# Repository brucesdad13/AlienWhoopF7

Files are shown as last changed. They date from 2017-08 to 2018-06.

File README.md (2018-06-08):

IMAGE AlienWhoop F7 Flight Controller Welcome

# AlienWhoopF7 Features :alien:
AlienWhoop flight controller for Tiny Whoop, Blade Inductrix, Eachine, BetaFPV, and other micro brushed quadcopter frames. Best in class flight controller running BetaFlight or Butterflight--surface mount soldering required.

* Choice of the top performing ARM processors: 
  * High-performance ST Microelectronics ARM Cortex-M4 core F4 168 MHz CPU
  * High-performance ST Microelectronics ARM Cortex-M7 core F7 216 MHz CPU
* Choice of top performing motion processors: 
  * Invensense MPU-6500 Six-Axis (Gyro + Accelerometer) low power consumption MEMS MotionTracking™ Device
  * Invensense MPU-9250 Nine-Axis (Gyro + Accelerometer + Compass) low power consumption MEMS MotionTracking™ Device
* Latest BetaFlight firmware running the ALIENWHOOPF4 target
* Butterflight firmware supported (iNav under final testing)
* Overkill power MOSFETs capable of extreme brushed motor insanity (6mm, 7mm, 8mm, 8.5mm, and 10mm coreless scream)
* Multiple UARTs for receivers and other devices (e.g. LED strip, beeper)
* Dedicated UART with inverter for FrSky and Futaba SBUS
* UART pads on top conveniently located for SmartAudio VTX control
* Blackbox logging via onboard dataflash chip
* Note: pilots must supply external receiver. Officially supporting FrSky XM, XM+, R-XSR (SBUS,F.PORT), LemonRX DSM2 and DSMX (SBUS), and FlySky FS-A8S (iBUS) satellites.
* 0.8mm 2oz Copper ENIG (gold) finish purple PCBs from OSH Park recommended

## DIY Flight Controller :alien:
If you fancy doing it yourself (DIY), and have the right equipment and patience, building an AlienWhoop from scratch can be tremendously satisfying--though not for the faint of heart. After doing your homework the first step is to place an order for blank PCBs from [OSH Park](https://oshpark.com/shared_projects/p4hs6DbI):
* We recommend ordering the 2oz copper 0.8mm thickness PCB
  * *It takes about three weeks to make the thin boards which allows plenty of time to order components from the bill of materials in the resources folder.*
  * **Please note there are slight changes to the bill of materials (BOM) depending which MCU you choose (F4 vs F7). These MCUs are not 100% pin compatible.**
   * F4: components C7 and C10 place 4.7uF ceramic capacitors and C15 substitute 0 ohm resistor (0R).
   * F7: components C7, C10, and C15 place 4.7uF ceramic capacitor.

## Official AlienWhoop pages :alien:
AlienWhoop has many ways for you to stay engaged. Please Like and/or Follow Us for regular updates in your status feed related to AlienWhoop, DIY electronics, and micro brushed quadcopter related posts.
* http://fb.me/alienwhoop/ Facebook
* http://alienwhoop.us/ News and products
* http://alienwhoop.us/git-config CLI diff files for Betaflight and Butterflight
* http://alienwhoop.us/discord Join our Discord chat and hang out with the community or ask questions

## See the AlienWhoop in action on YouTube :alien:

IMAGE VelcroFPV Tinywhoop Invitational 2018 Best Run (https://www.youtube.com/watch?v=_v07IYvKqXY)

IMAGE VelcroFPV AlienWhoop Build (https://www.youtube.com/watch?v=SfvL05S8X-s&t=30s)

May this work be of benefit and bring much joy and happiness!

## Acknowledgements :alien:

AlienWhoop V2.1 Dev Team:
* Charles Stevenson (brucesdad13)
* Travis Schrock (NotFastEnuf)
* Brian Pichardo (VelcroFPV)
* Michael Montiverdi (MontiFPV)

Deep bows of appreciation and thanks to Lance for his original work and tremendous
generosity in releasing his labor of love for the benefit of all flight controller
enthusiasts. Check out AlienWhoop's ancestry in our preserved copy of Lance's original AlienFlight
github repository of open source hardware flight controllers: the [Classic FC aka Classic Narrow](https://github.com/brucesdad13/AlienFlightArchive/blob/master/Flight-Controllers/Classic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), [F3 Quad FC](https://github.com/brucesdad13/AlienFlightArchive/blob/master/Flight-Controllers/F3-V1/F3-Quad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), [F3 Hexa FC](https://github.com/brucesdad13/AlienFlightArchive/blob/master/Flight-Controllers/F3-V1/F3-Hexa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), and [F3 Octo FC](https://github.com/brucesdad13/AlienFlightArchive/blob/master/Flight-Controllers/F3-V1/F3-Octo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).
*As of late July 2017, the original www.alienflight.com site is no longer in operation.

Equally deep bows to Jesse Perkins, creator of Tiny Whoop, and the source of inspiration and love for tiny brushed quads.
* http://www.tinywhoop.com/ ~
* https://www.facebook.com/groups/tinywhoop/ ~

~ Please note: **AlienWhoop** is not affiliated with nor endorsed by AlienFlight or forks of Lance's work such as AlienFlight NG. The use of Alien in the name and the alien head vector graphic used on the board silkscreen are nods to the lineage of this remix and to the work of Lance and others who created the conditions for this project to arise. Likewise, AlienWhoop is not affiliated with nor endorsed by Tiny Whoop. The Whoop in the name comes from Jesse Perkin's fantastic Tiny Whoop ("a small first-person-view aircraft that truly allows you to feel the gift of flight and the feeling of being tiny" [tinywhoop.com]) and is simply a nod to his efforts and the TW community worldwide.

## If you like this project and want to support further development
* https://paypal.me/AlienWhoop/ <a href="https://paypal.me/AlienWhoop/">Donate PayPal - The safer, easier way to pay online!</a>
* http://shop.alienwhoop.us/ for t-shirts and gear

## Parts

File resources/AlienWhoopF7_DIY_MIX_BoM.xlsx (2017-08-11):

Value | Device | Package | Parts/Silkscreen Label | Description | MF | MPN
.01uF | Capacitor 0.01 uF | 0603 | C3 | CAPACITOR | Murata | GRM188R71C103KA01D
.1uF | Capacitor 0.10 uF | 0603 | C2, C5, C6, C8, C9, C11, C12, C14 | CAPACITOR | Murata | GRM188R71C104KA01D
10uF | Capacitor 10.0 uF | 0805 | C1, C4 | CAPACITOR | Taiyo Yuden | JMK212AB7106KG-T
1uF | Capacitor 1.00 uF | 0603 | C13 | CAPACITOR | Murata | GRM188R71C105KA12D
4.7uF | Capacitor 4.70 uF | 0603 | C7, C10 | CAPACITOR | Murata | GRJ188C70J475KE11D
4.7uF | Capacitor 4.70 uF | 0603 | C15 | CAPACITOR | Murata | GRJ188C70J475KE11D
FDMA410NZ | MOSFET | UMLP-6 | Q2, Q3, Q4, Q5 | MOSFET 20V Single N-Ch 1.5V (9.5 amp continuous, 23 amp pulsed) | Fairchild | FDMA410NZ
1S (3.8V) | Connector JST PH 2.0 | S2B-PH-K-S | BAT | 1S LIPO connector to make PowerWhoop 2.0 pigtail w/24AWG wire and heatshrink | JST | S2B-PH-K-S
SBUS | Connector 3-pin Receiver | S3B-ZR | RX | 3 Pin Receiver (optional.. Used if not directly soldering satellite rx to through holes) | JST | S3B-ZR
105133-0011 | Vertical USB Port | 1051330011-SD | USB | Molex USB Connectors uUSB B Rec Vertical TH 2.30 | MOLEX | 105133-0011
IRLML6402 | MOSFET-P | SOT-23 | Q1 | P-Channel MOSFET | IR | IRLML6402
MPU-6500 | MPU-6500 Gyro/Acc | QFN24_PAD | U2 | Invensense MPU-6500 6-axis motion processor gyro accelerometer NO COMPASS | INVENSENSE | MPU-6500
MPU-9250 | MPU-9250 Gyro/Acc/Mag | QFN24_PAD | U2 | Invensense MPU-9250 9-axis motion processor gyro accelerometer compass | INVENSENSE | MPU-9250
2.2uH | Inductor 2.2 uH | TFM201610ALMA | L1 | Thin Film Metal Inductor substituted for Taiyo Yuden | Taiyo Yuden | TFM201610ALMA2R2MTAA
53047-0210 | Connector Brushed Motor | PICO-53047-02 | M1, M2, M3, M4 | Motor Connector | MOLEX | 53047-0210
0R | Resistor 0.00 Ohms | 0603 | C15 | RESISTOR used as Jumper | Yageo | RC0603FR-070RL
0R | Resistor 0.00 Ohms | 0603 | C7, C10 | RESISTOR used as Jumper | Yageo | RC0603FR-070RL
10K | Resistor 10K Ohms | 0603 | R1, R2, R3, R4, R5 | RESISTOR | Vishay | CRCW060310K0FKEAHP
8mhz | Resonator 8 MHz | RESONATOR_8 | Y1 | SMD Ceramic Resonators | Murata | CSTCE8M00G55-R0
BLUE | LED (blue as spec'd only!) | 0805 | LED0, LED1, PWR | SMD CHIP LED | Kingbright | APHCM2012QBC/D-F01
STM32F4/F7 | STM32F405RGT | LQFP64 | IC1 | ARM 32-bit Cortex™-M3 168 MHz CPU |  | STM32F405RGT6
STM32F4/F7 | STM32F722RET | LQFP64 | IC1 | ARM 32-bit Cortex™-M4 216 MHz CPU |  | STM32F722RET6
TPS63001 | TPS630XX-TPS63001 | VSON-N10 | U1 | Buck/Boost Converter | TI | TPS63001DRCR
AW-F4-BR-V2-PCB | AW-F4-BR-V2-PCB | PCB | PCB | PCB 0.8mm thick 2oz copper | OSH Park | AlienWhoop F7 DIY MIX
* Yellow highlighted rows are for F4 builds or in case of MPU-9250 optional upgrade for compass/mag
** LED circuits lack current limiting resistor so only specified blue LED can be used for LED0 and LED1

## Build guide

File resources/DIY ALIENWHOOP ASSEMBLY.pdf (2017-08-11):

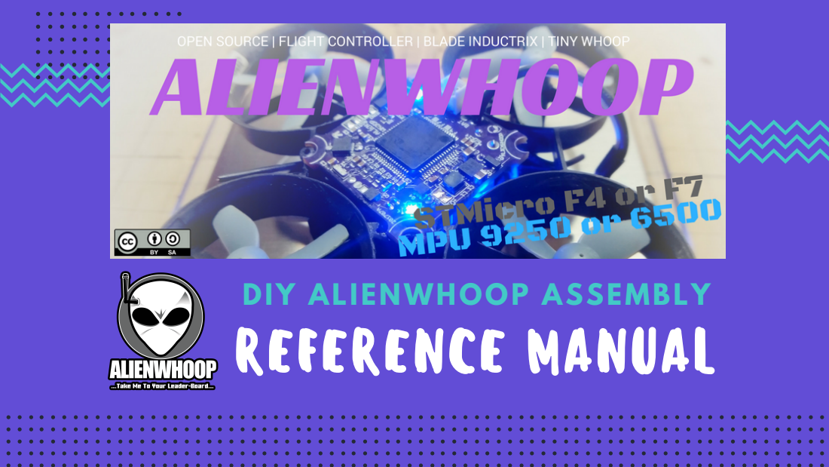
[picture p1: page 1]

DIY ALIENWHOOP ASSEMBLY
REFERENCE MANUAL

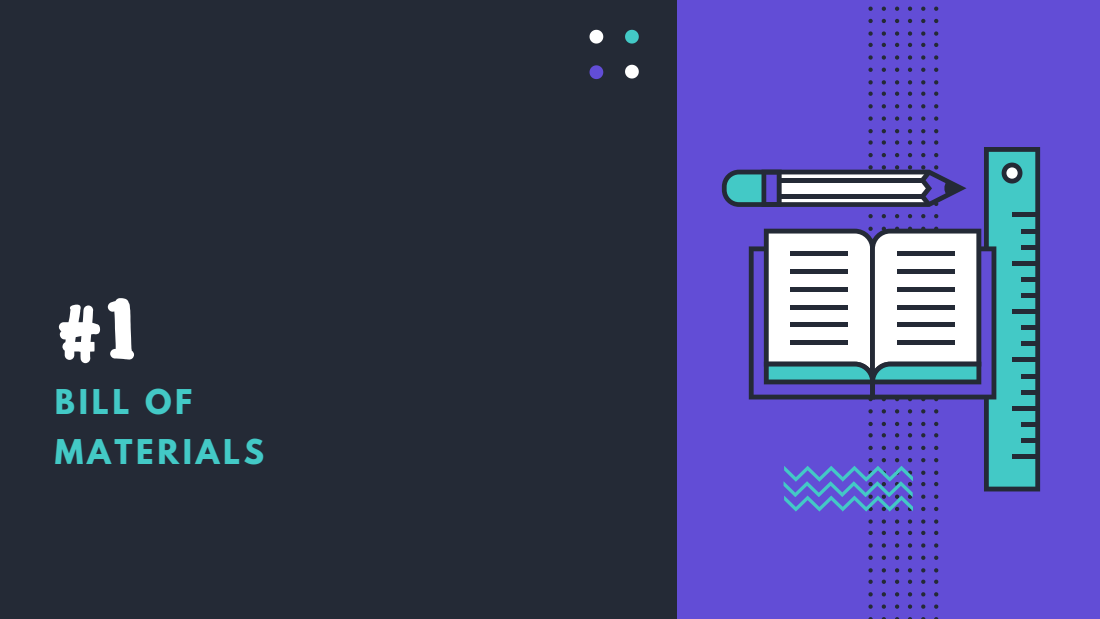
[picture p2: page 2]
BILL OF MATERIALS

# CHECK YOUR CART

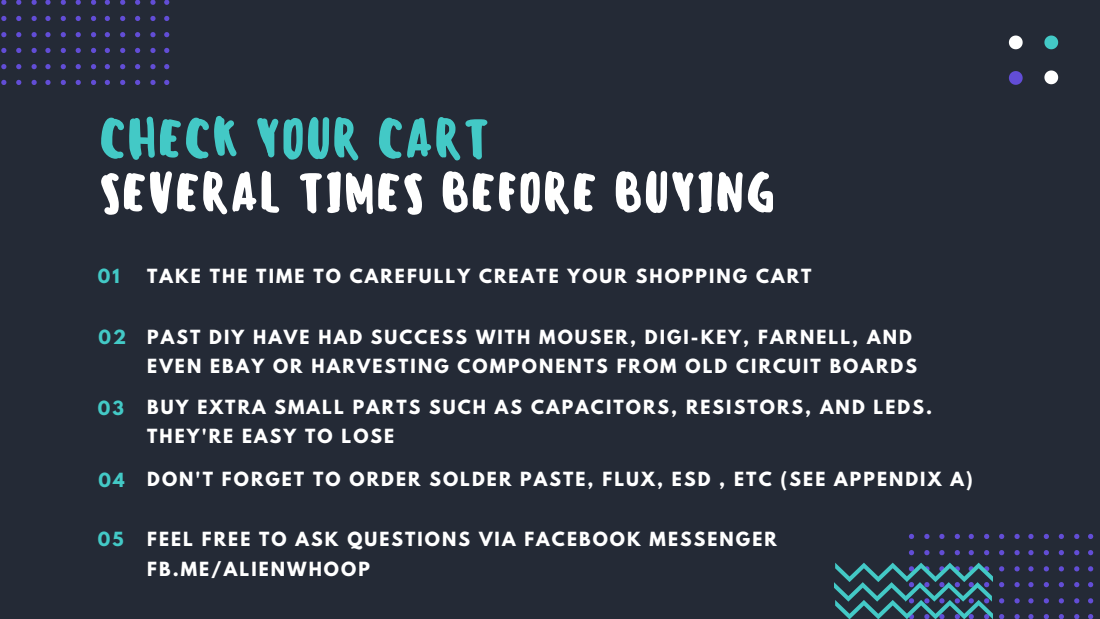
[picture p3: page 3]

SEVERAL TIMES BEFORE BUYING

01 TAKE THE TIME TO CAREFULLY CREATE YOUR SHOPPING CART

PAST DIY HAVE HAD SUCCESS WITH MOUSER, DIGI -KEY, FARNELL, AND
EVEN EBAY OR HARVESTING COMPONENTS FROM OLD CIRCUIT BOARDS
BUY EXTRA SMALL PARTS SUCH AS CAPACITORS, RESISTORS, AND LEDS.
THEY'RE EASY TO LOSE

04 DON'T FORGET TO ORDER SOLDER PASTE, FLUX, ESD , ETC (SEE APPENDIX A)

FEEL FREE TO ASK QUESTIONS VIA FACEBOOK MESSENGER
FB.ME/ALIENWHOOP

# Bill of Materials

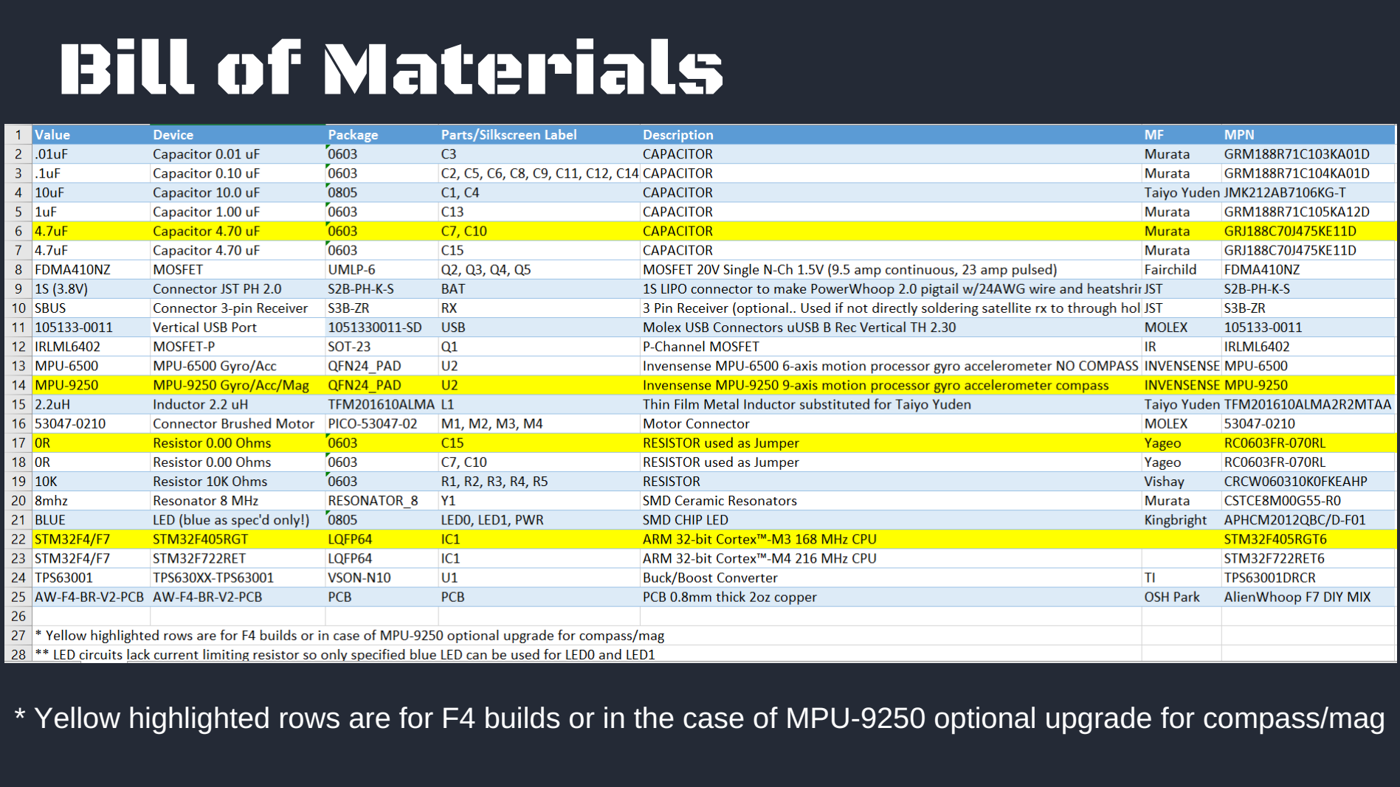
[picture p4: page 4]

* Yellow highlighted rows are for F4 builds or in the case of MPU-9250 optional upgrade for compass/mag

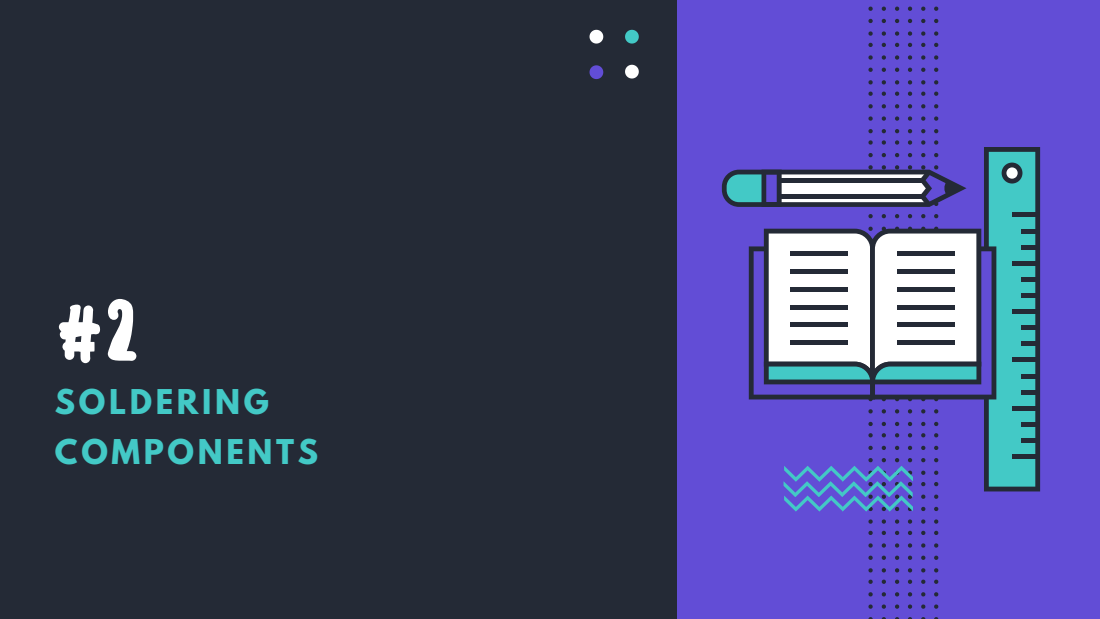
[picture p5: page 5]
SOLDERING COMPONENTS

T

O

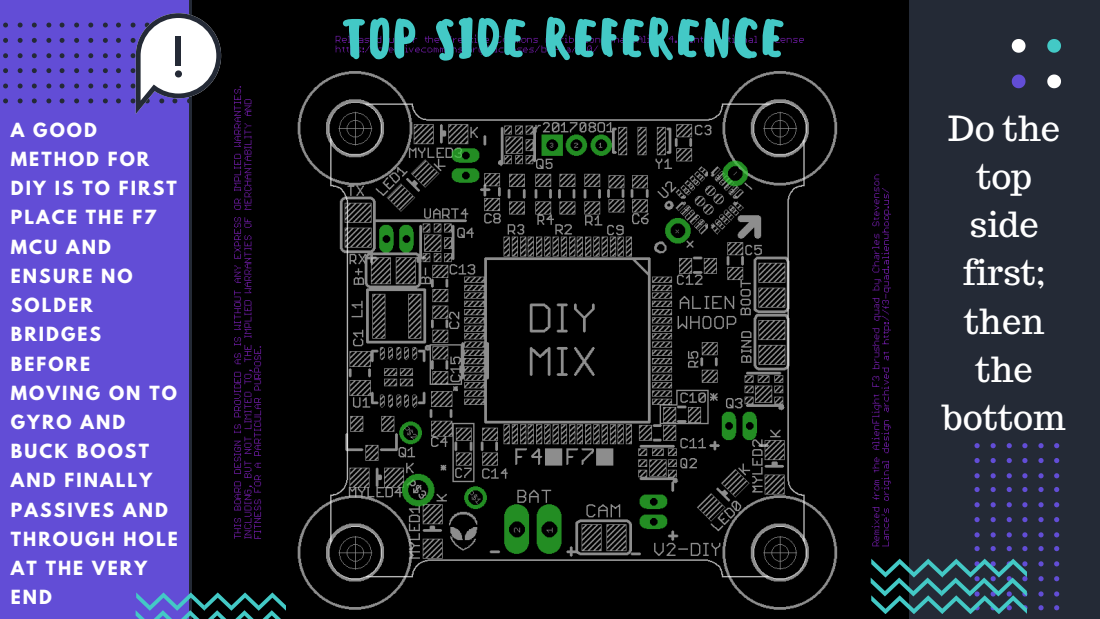
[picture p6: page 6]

B
O

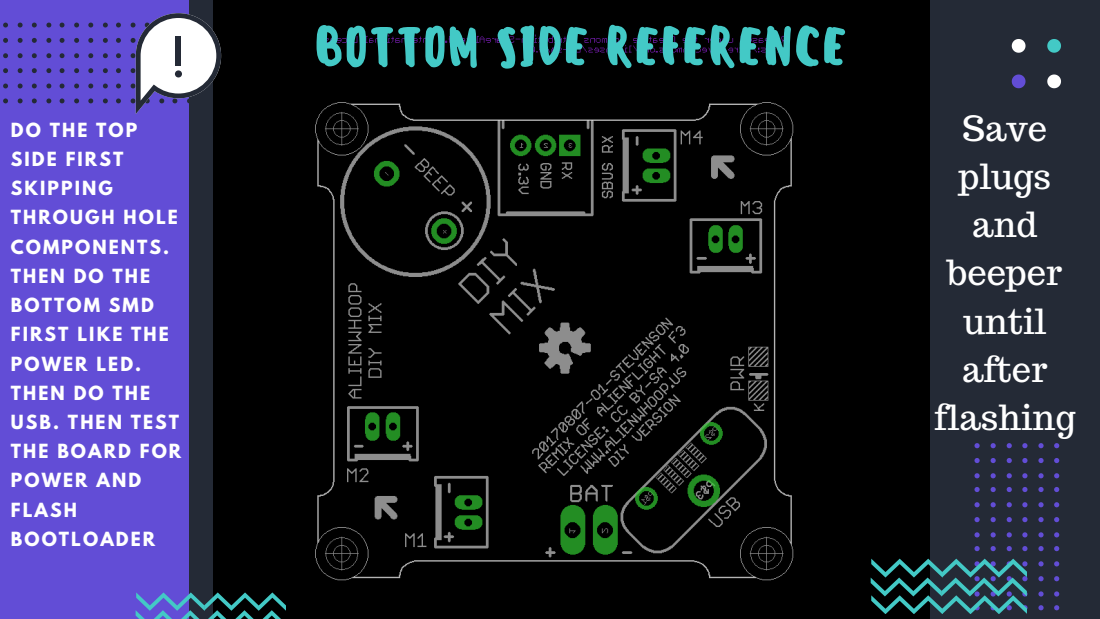
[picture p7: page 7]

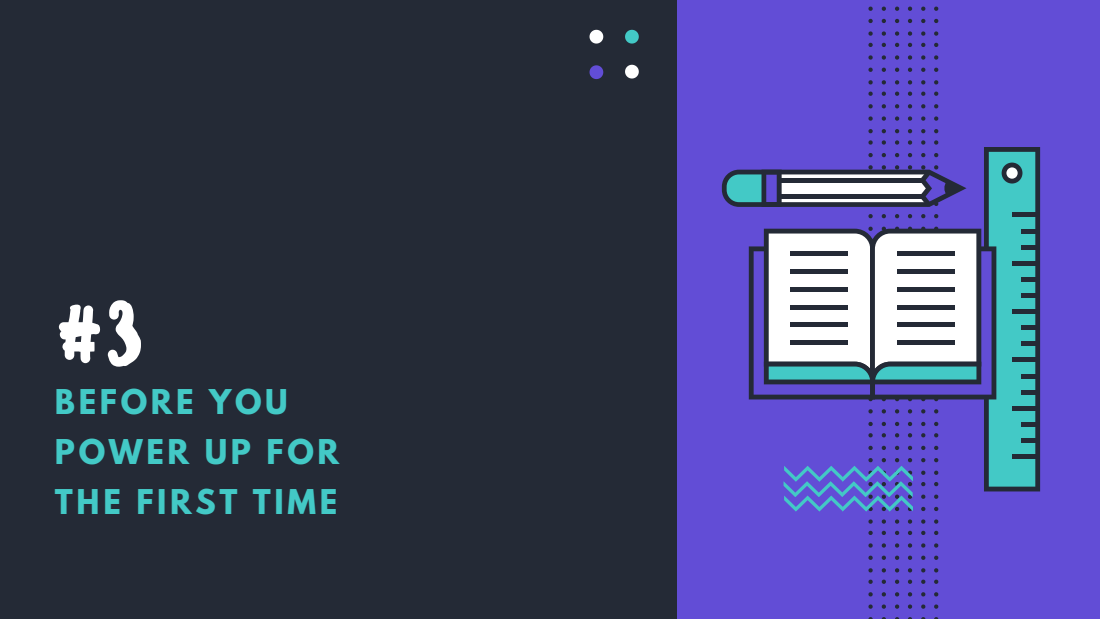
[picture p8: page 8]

BEFORE YOU
POWER UP FOR
THE FIRST TIME

# CHECK FOR SOLDER

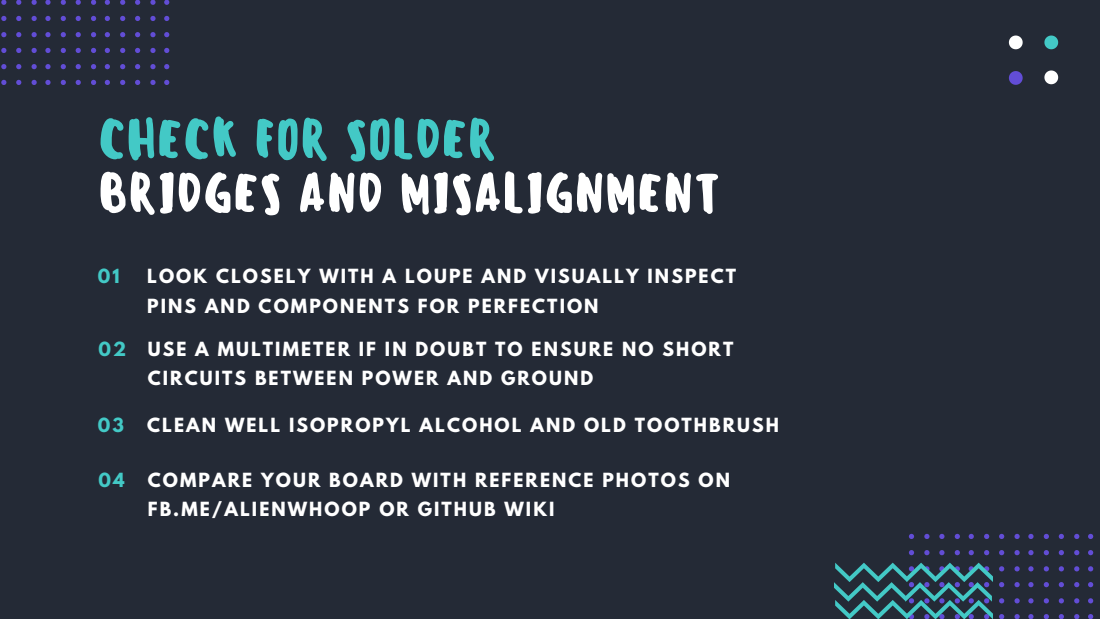
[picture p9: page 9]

BRIDGES AND MISALIGNMENT

LOOK CLOSELY WITH A LOUPE AND VISUALLY INSPECT
PINS AND COMPONENTS FOR PERFECTION

USE A MULTIMETER IF IN DOUBT TO ENSURE NO SHORT
CIRCUITS BETWEEN POWER AND GROUND

03 CLEAN WELL ISOPROPYL ALCOHOL AND OLD TOOTHBRUSH

COMPARE YOUR BOARD WITH REFERENCE PHOTOS ON
FB.ME/ALIENWHOOP OR GITHUB WIKI

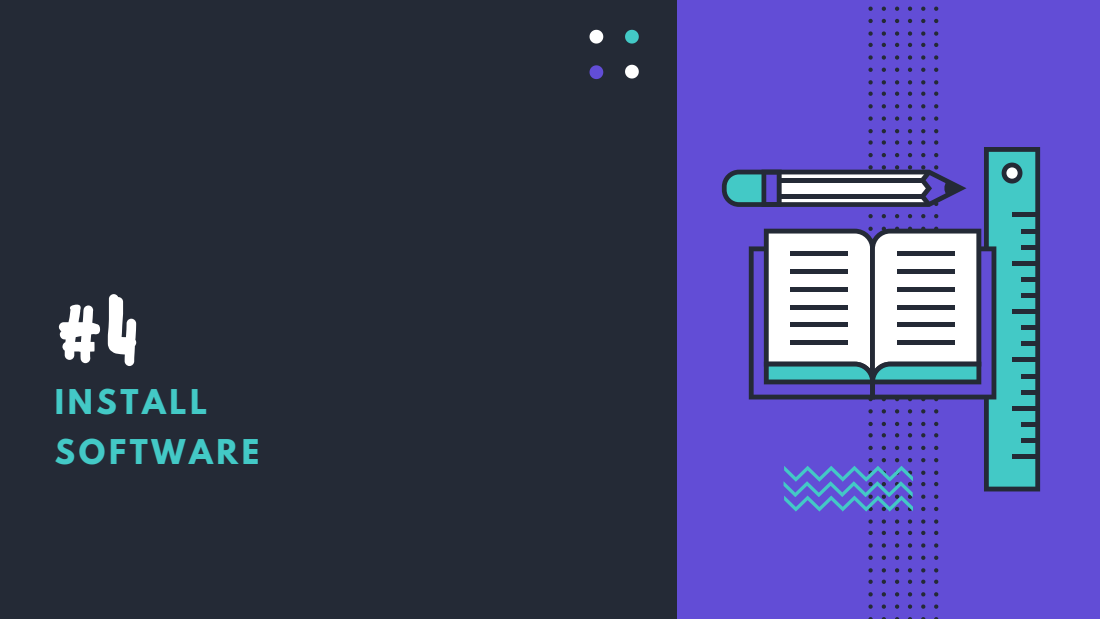
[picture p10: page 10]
INSTALL SOFTWARE

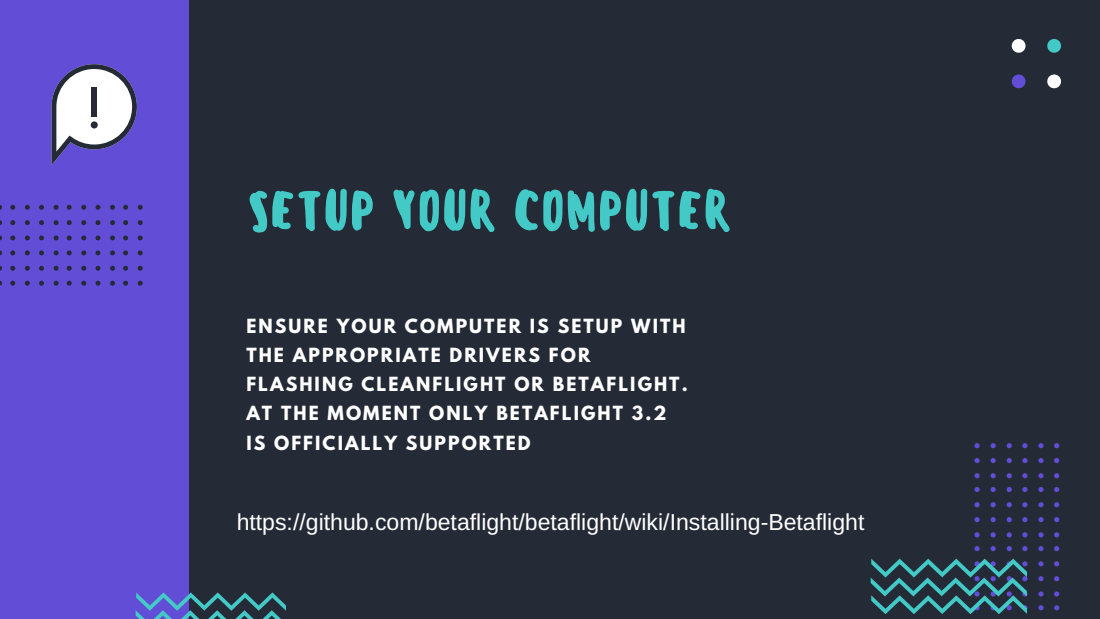
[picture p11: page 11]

SETUP YOUR COMPUTER

ENSURE YOUR COMPUTER IS SETUP WITH
THE APPROPRIATE DRIVERS FOR
FLASHING CLEANFLIGHT OR BETAFLIGHT.
AT THE MOMENT ONLY BETAFLIGHT 3.2
IS OFFICIALLY SUPPORTED

https://github.com/betaflight/betaflight/wiki/Installing-Betaflight

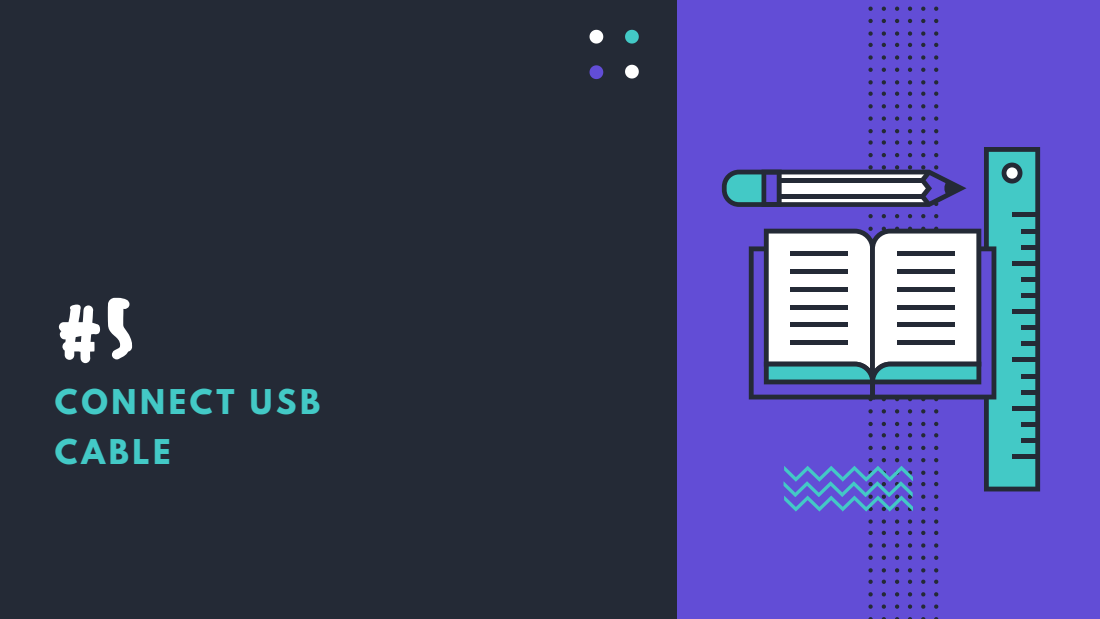
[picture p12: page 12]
CONNECT USB CABLE

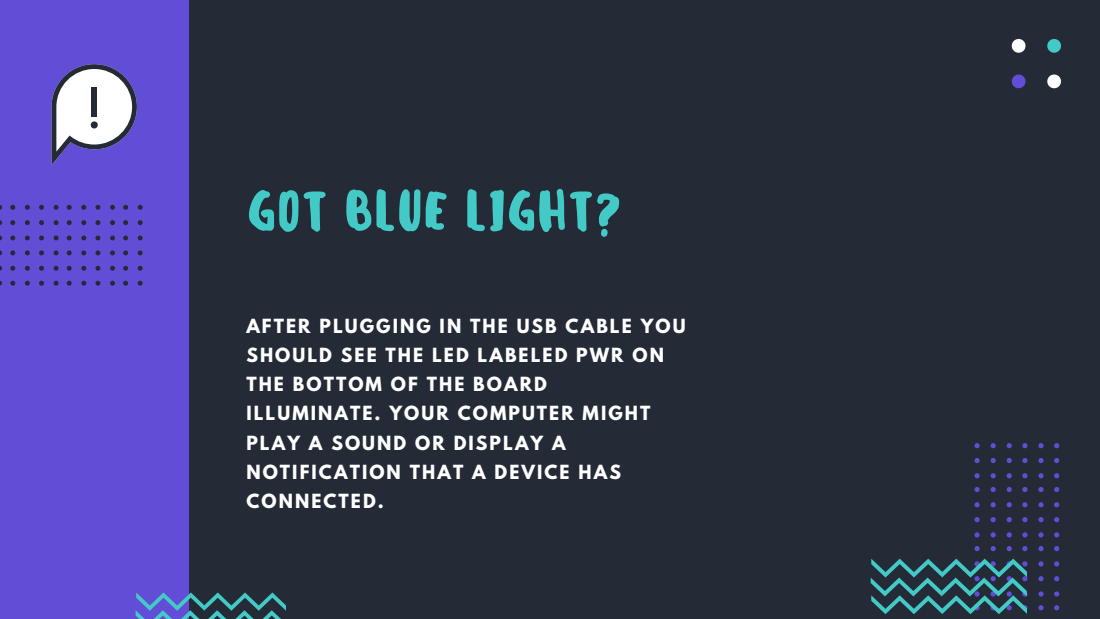
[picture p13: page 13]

GOT BLUE LIGHT?

AFTER PLUGGING IN THE USB CABLE YOU
SHOULD SEE THE LED LABELED PWR ON
THE BOTTOM OF THE BOARD
ILLUMINATE. YOUR COMPUTER MIGHT
PLAY A SOUND OR DISPLAY A
NOTIFICATION THAT A DEVICE HAS
CONNECTED.

# FLASHING BETAFLIGHT

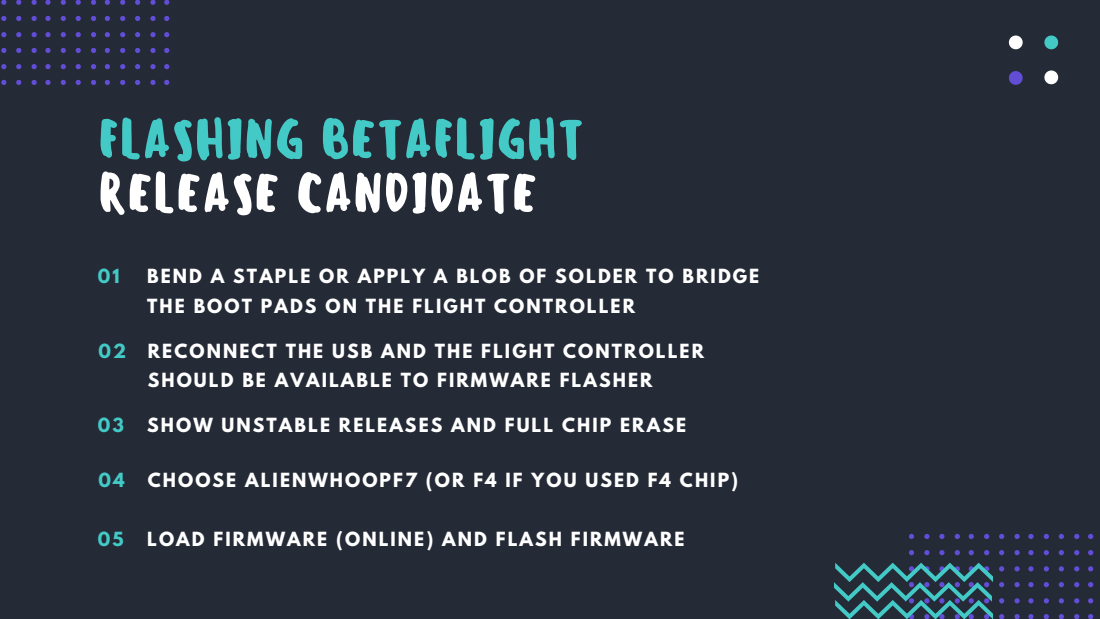
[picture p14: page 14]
RELEASE CANDIDATE

BEND A STAPLE OR APPLY A BLOB OF SOLDER TO BRIDGE
THE BOOT PADS ON THE FLIGHT CONTROLLER

RECONNECT THE USB AND THE FLIGHT CONTROLLER
SHOULD BE AVAILABLE TO FIRMWARE FLASHER

03 SHOW UNSTABLE RELEASES AND FULL CHIP ERASE

04 CHOOSE ALIENWHOOPF7 (OR F4 IF YOU USED F4 CHIP)

05 LOAD FIRMWARE (ONLINE) AND FLASH FIRMWARE

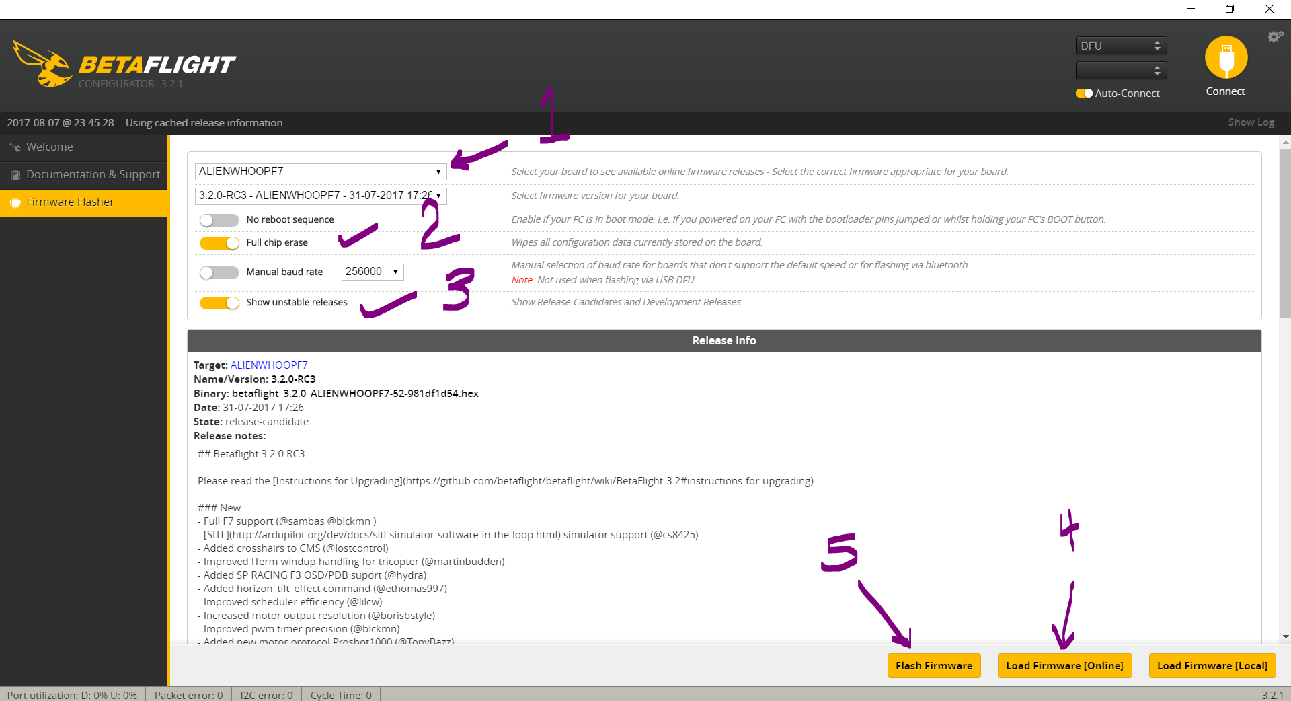
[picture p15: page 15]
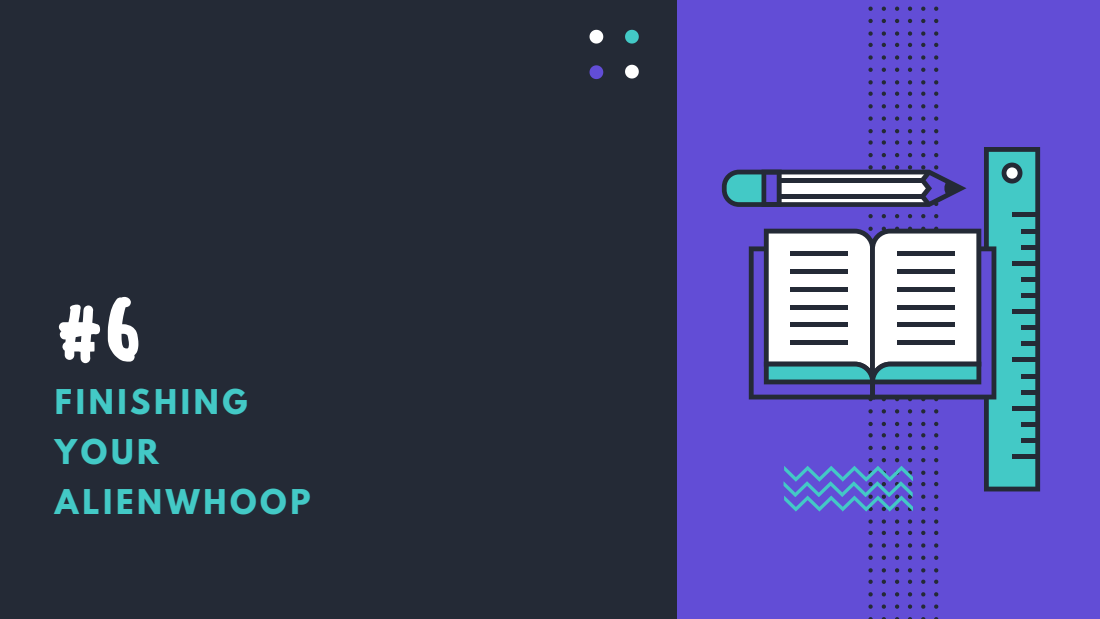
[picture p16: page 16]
FINISHING YOUR ALIENWHOOP

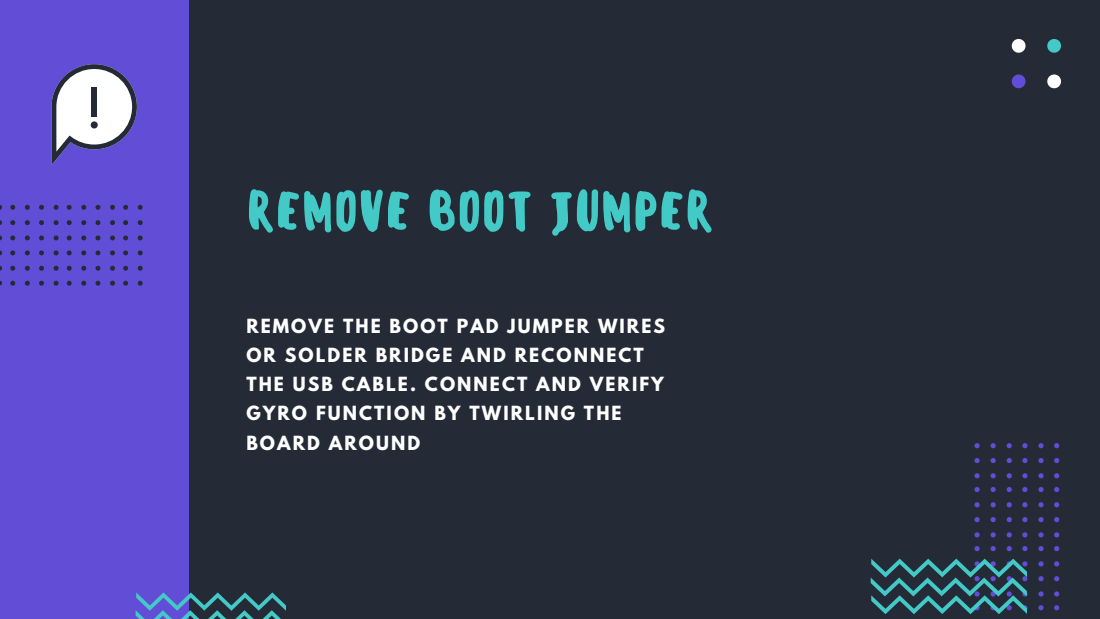
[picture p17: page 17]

REMOVE BOOT JUMPER

REMOVE THE BOOT PAD JUMPER WIRES
OR SOLDER BRIDGE AND RECONNECT
THE USB CABLE. CONNECT AND VERIFY
GYRO FUNCTION BY TWIRLING THE
BOARD AROUND

# FINISHING UP

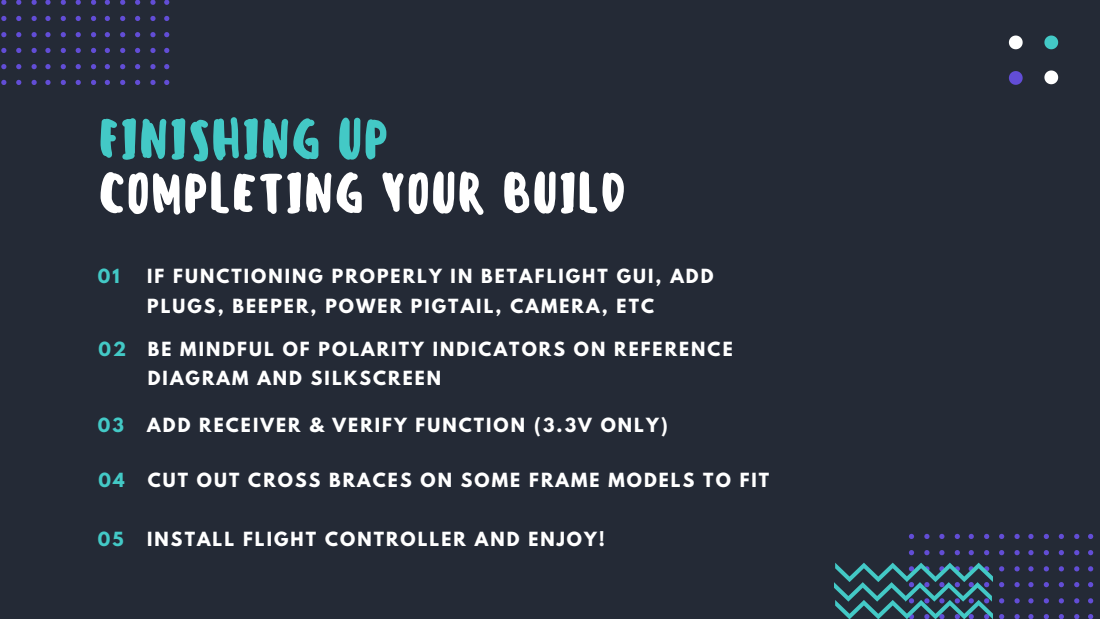
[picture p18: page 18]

COMPLETING YOUR BUILD

IF FUNCTIONING PROPERLY IN BETAFLIGHT GUI, ADD
PLUGS, BEEPER, POWER PIGTAIL, CAMERA, ETC

BE MINDFUL OF POLARITY INDICATORS ON REFERENCE
DIAGRAM AND SILKSCREEN

03 ADD RECEIVER & VERIFY FUNCTION (3.3V ONLY)

04 CUT OUT CROSS BRACES ON SOME FRAME MODELS TO FIT

05 INSTALL FLIGHT CONTROLLER AND ENJOY!

# APPENDIX A

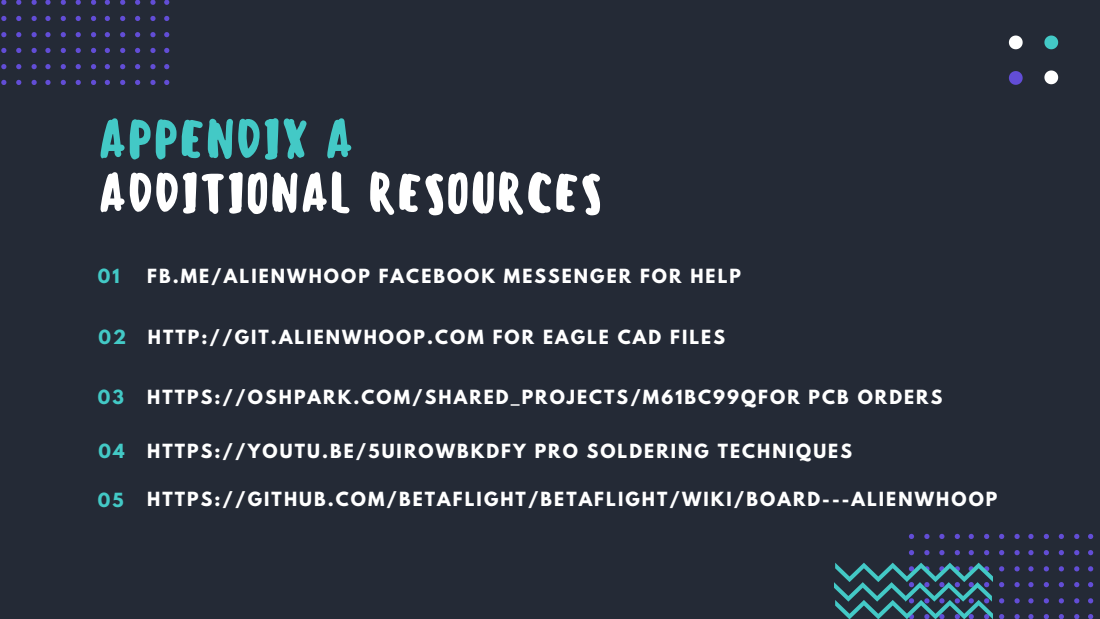
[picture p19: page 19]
ADDITIONAL RESOURCES

01 FB.ME/ALIENWHOOP FACEBOOK MESSENGER FOR HELP

02 HTTP://GIT.ALIENWHOOP.COM FOR EAGLE CAD FILES

03 HTTPS://OSHPARK.COM/SHARED_PROJECTS/M61BC99QFOR PCB ORDERS

04 HTTPS://YOUTU.BE/5UIROWBKDFY PRO SOLDERING TECHNIQUES

05 HTTPS://GITHUB.COM/BETAFLIGHT/BETAFLIGHT/WIKI/BOARD- - -ALIENWHOOP

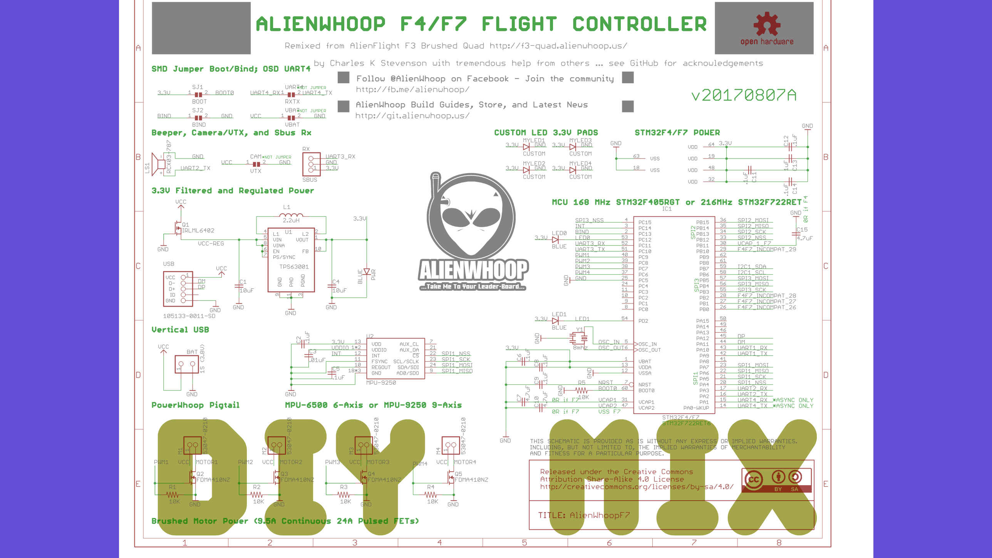
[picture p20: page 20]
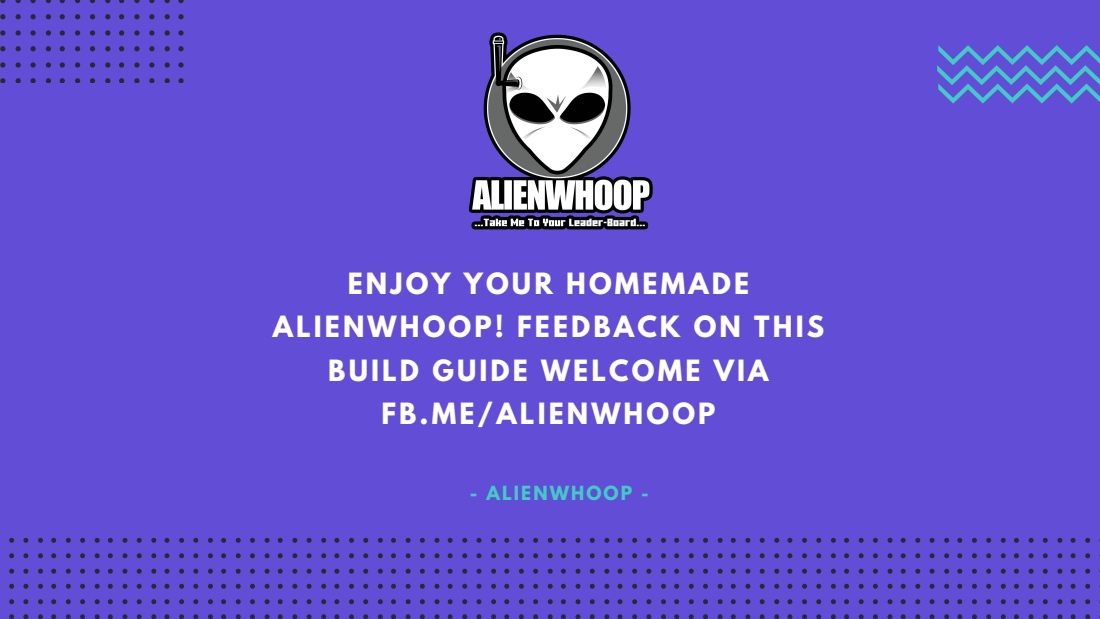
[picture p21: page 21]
- ALIENWHOOP -

ENJOY YOUR HOMEMADE
ALIENWHOOP! FEEDBACK ON THIS
BUILD GUIDE WELCOME VIA
FB.ME/ALIENWHOOP

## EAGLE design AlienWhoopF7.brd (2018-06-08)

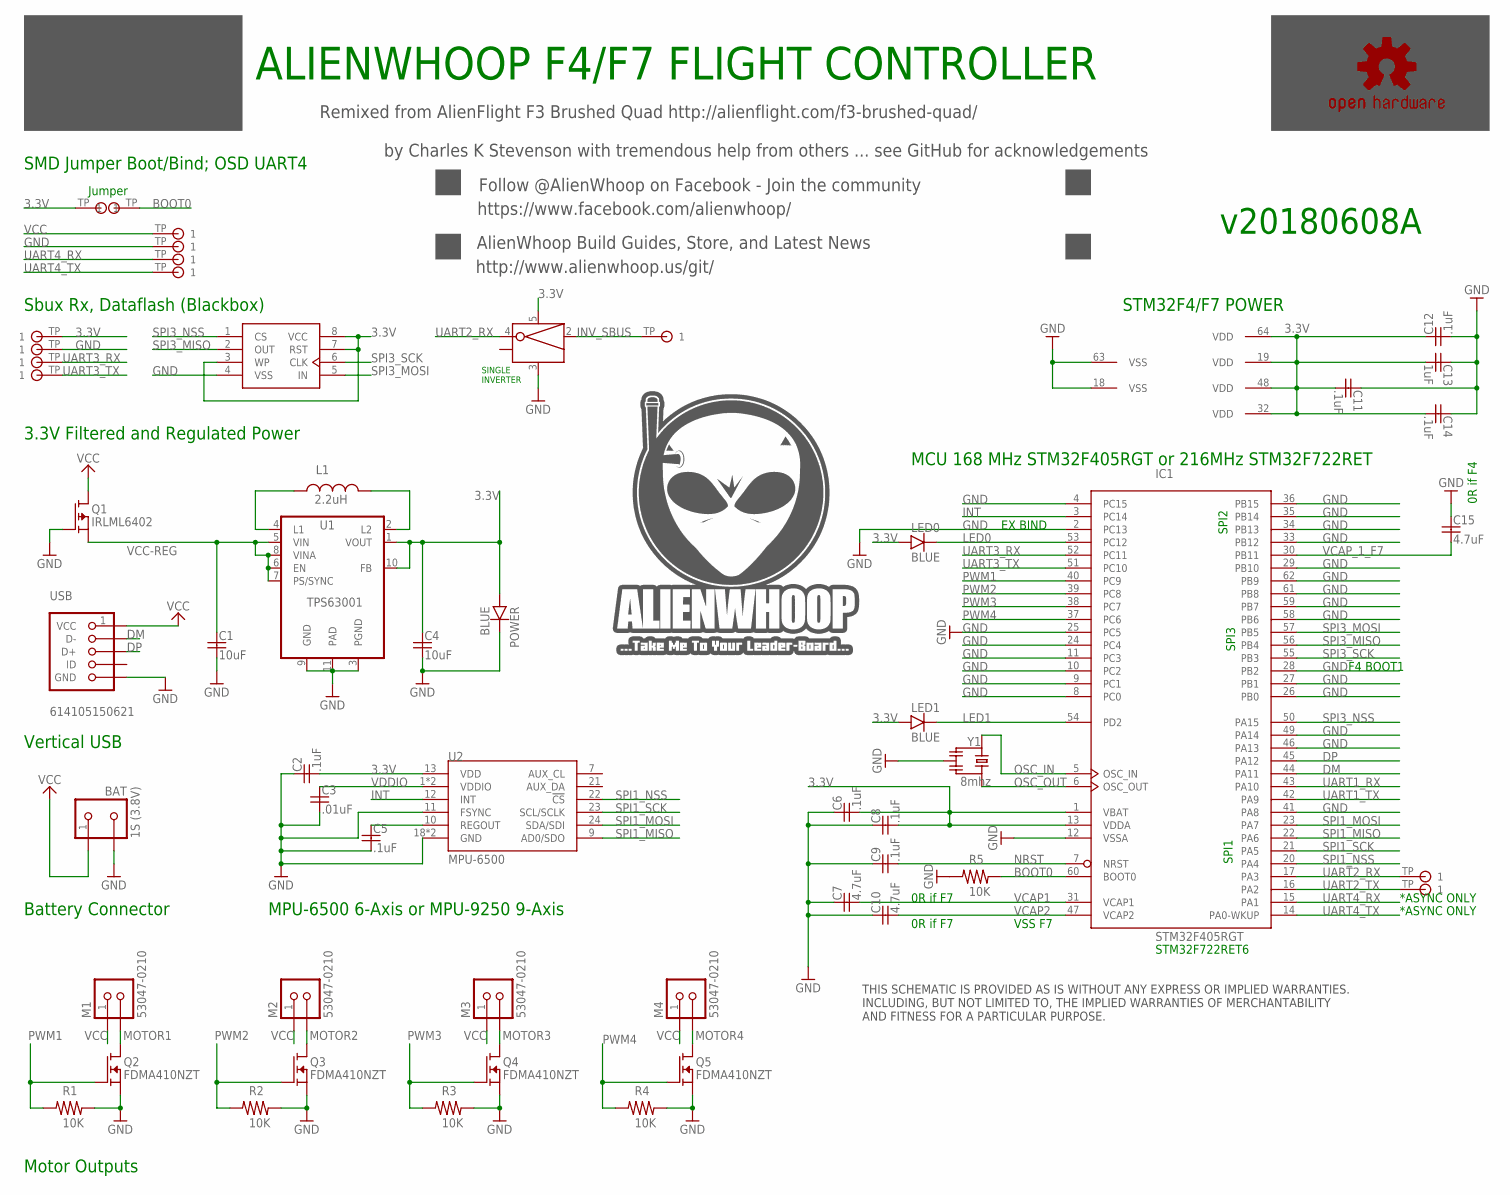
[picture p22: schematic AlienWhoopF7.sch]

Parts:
3.3V, 3V3: TESTPAD; PARTNO TESTPAD
BAT: 1S (3.8V); S2B-PH-K-S
BOOT: TESTPAD; PARTNO TESTPAD
C1, C4: 10uF; YUDEN-CAP-0805
C2, C5, C6, C8, C9, C11, C12, C14: .1uF; MUR-CAP-0603
C3: .01uF; MUR-CAP-0603
C7, C10, C15: 4.7uF; MUR-CAP-0603
C13: 1uF; MUR-CAP-0603
GND: TESTPAD; PARTNO TESTPAD
GND@1: TESTPAD; PARTNO TESTPAD
IC1: STM32F405RGT; LQFP64; MPN STM32F045RGT
L1: 2.2uH; DFE201612E-2R2M-P2; PARTNO DFE201612E-2R2M-P2
LED0, LED1: BLUE; SMD-CHIP-LED-0805
LOGO3: OSHW-LOGOS; OSHW-LOGO-S; PARTNO OSHW-LOGOS
M1, M2, M3, M4: 53047-0210; PICO-53047-02
POWER: BLUE; SMD-CHIP-LED-0805
Q1: IRLML6402; SOT-23
Q2, Q3, Q4, Q5: FDMA410NZT; MICROFET-2X2; PARTNO FDMA410NZT
R1, R2, R3, R4, R5: 10K; VISH-RES-0603
RX2, RX2/INV, RX3, RX4: TESTPAD; PARTNO TESTPAD
TX2, TX3, TX4: TESTPAD; PARTNO TESTPAD
U1: TPS63001; VSON-N10
U2: MPU-6500; QFN24_PAD; PARTNO MPU-6500
U3: MX25L6406EM2I-12G; M25P32; PARTNO MX25L6406EM2I-12G
U4: SN74LVC1G04DBVR; SOT23-5; PARTNO SN74LVC1G04DBVR
USB: 614105150621; USB-BFPV; PARTNO 614105150621
VCC@1: TESTPAD; PARTNO TESTPAD
Y1: 8mhz; RESONATOR_8

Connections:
3.3V: 3.3V.TP, 3V3.TP, C2.2, C4.1, C6.2, C8.2, C11.2, C12.1, C13.2, C14.2, IC1.1 (VBAT), IC1.13 (VDDA), IC1.19 (VDD), IC1.32 (VDD), IC1.48 (VDD), IC1.64 (VDD), LED0.A, LED1.A, POWER.A, U1.1 (VOUT), U1.10 (FB), U2.13 (VDD), U3.3 (WP), U3.7 (RST), U3.8 (VCC), U4.5 (VCC)
BOOT0: BOOT.TP, IC1.60 (BOOT0), R5.1
DM: IC1.44 (PA11), USB.2 (D-)
DP: IC1.45 (PA12), USB.3 (D+)
GND: BAT.2, C1.2, C2.1, C3.2, C4.2, C5.2, C6.1, C7.1, C8.1, C9.1, C10.1, C11.1, C12.2, C13.1, C14.1, C15.1, GND.TP, GND@1.TP, IC1.2 (PC13), IC1.4 (PC15), IC1.8 (PC0), IC1.9 (PC1), IC1.10 (PC2), IC1.11 (PC3), IC1.12 (VSSA), IC1.18 (VSS), IC1.24 (PC4), IC1.25 (PC5), IC1.26 (PB0), IC1.27 (PB1), IC1.28 (PB2), IC1.29 (PB10), IC1.33 (PB12), IC1.34 (PB13), IC1.35 (PB14), IC1.36 (PB15), IC1.41 (PA8), IC1.46 (PA13), IC1.49 (PA14), IC1.58 (PB6), IC1.59 (PB7), IC1.61 (PB8), IC1.62 (PB9), IC1.63 (VSS), POWER.C, Q1.1 (G), Q2.S, Q2.S1 (S), Q3.S, Q3.S1 (S), Q4.S, Q4.S1 (S), Q5.S, Q5.S1 (S), R1.1, R2.1, R3.1, R4.1, R5.2, U1.3 (PGND), U1.9 (GND), U1.11 (PAD), U2.11 (FSYNC), U2.18 (GND), U2.20 (GND), U3.4 (VSS), U4.3 (GND), USB.5 (GND), USB.P$6 (GND), USB.P$7 (GND), Y1.2
INT: IC1.3 (PC14), U2.12 (INT)
INV_SBUS: RX2/INV.TP, U4.2 (A)
L1: L1.P$1 (1), U1.4 (L1)
L2: L1.P$2 (2), U1.2 (L2)
LED0: IC1.53 (PC12), LED0.C
LED1: IC1.54 (PD2), LED1.C
MOTOR1: M1.2, Q2.D, Q2.D1 (D), Q2.D2 (D), Q2.D3 (D), Q2.D4 (D)
MOTOR2: M2.2, Q3.D, Q3.D1 (D), Q3.D2 (D), Q3.D3 (D), Q3.D4 (D)
MOTOR3: M3.2, Q4.D, Q4.D1 (D), Q4.D2 (D), Q4.D3 (D), Q4.D4 (D)
MOTOR4: M4.2, Q5.D, Q5.D1 (D), Q5.D2 (D), Q5.D3 (D), Q5.D4 (D)
NRST: C9.2, IC1.7 (NRST)
OSC_IN: IC1.5 (OSC_IN), Y1.1
OSC_OUT: IC1.6 (OSC_OUT), Y1.3
PWM1: IC1.40 (PC9), Q2.G, R1.2
PWM2: IC1.39 (PC8), Q3.G, R2.2
PWM3: IC1.38 (PC7), Q4.G, R3.2
PWM4: IC1.37 (PC6), Q5.G, R4.2
REGOUT: C5.1, U2.10 (REGOUT)
SPI1_MISO: IC1.22 (PA6), U2.9 (AD0/SDO)
SPI1_MOSI: IC1.23 (PA7), U2.24 (SDA/SDI)
SPI1_NSS: IC1.20 (PA4), U2.22 (!CS)
SPI1_SCK: IC1.21 (PA5), U2.23 (SCL/SCLK)
SPI3_MISO: IC1.56 (PB4), U3.2 (OUT)
SPI3_MOSI: IC1.57 (PB5), U3.5 (IN)
SPI3_NSS: IC1.50 (PA15), U3.1 (CS)
SPI3_SCK: IC1.55 (PB3), U3.6 (CLK)
UART1_RX: IC1.43 (PA10)
UART1_TX: IC1.42 (PA9)
UART2_RX: IC1.17 (PA3), RX2.TP, U4.4 (Y)
UART2_TX: IC1.16 (PA2), TX2.TP
UART3_RX: IC1.52 (PC11), RX3.TP
UART3_TX: IC1.51 (PC10), TX3.TP
UART4_RX: IC1.15 (PA1), RX4.TP
UART4_TX: IC1.14 (PA0-WKUP), TX4.TP
VCAP1: C7.2, IC1.31 (VCAP1)
VCAP2: C10.2, IC1.47 (VCAP2)
VCAP_1_F7: C15.2, IC1.30 (PB11)
VCC: BAT.1, M1.1, M2.1, M3.1, M4.1, Q1.3 (D), USB.1 (VCC), VCC@1.TP
VCC-REG: C1.1, Q1.2 (S), U1.5 (VIN), U1.6 (EN), U1.7 (PS/SYNC), U1.8 (VINA)
VDDIO: C3.1, U2.1 (VDDIO), U2.8 (VDDIO)

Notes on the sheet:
THIS SCHEMATIC IS PROVIDED AS IS WITHOUT ANY EXPRESS OR IMPLIED WARRANTIES. INCLUDING, BUT NOT LIMITED TO, THE IMPLIED WARRANTIES OF MERCHANTABILITY AND FITNESS FOR A PARTICULAR PURPOSE.
Remixed from AlienFlight F3 Brushed Quad http://alienflight.com/f3-brushed-quad/
STM32F4/F7 POWER
MPU-6500 6-Axis or MPU-9250 9-Axis
Motor Outputs
VSS F7
0R if F7
0R if F4
Battery Connector
ALIENWHOOP F4/F7 FLIGHT CONTROLLER
Vertical USB
Sbux Rx, Dataflash (Blackbox)
3.3V Filtered and Regulated Power
STM32F722RET6
SMD Jumper Boot/Bind; OSD UART4
https://www.facebook.com/alienwhoop/
Follow @AlienWhoop on Facebook - Join the community
MCU 168 MHz STM32F405RGT or 216MHz STM32F722RET
by Charles K Stevenson with tremendous help from others ... see GitHub for acknowledgements
v20180608A
SPI1
SPI2
SPI3
*ASYNC ONLY
http://www.alienwhoop.us/git/
AlienWhoop Build Guides, Store, and Latest News
EX BIND
F4 BOOT1
Jumper

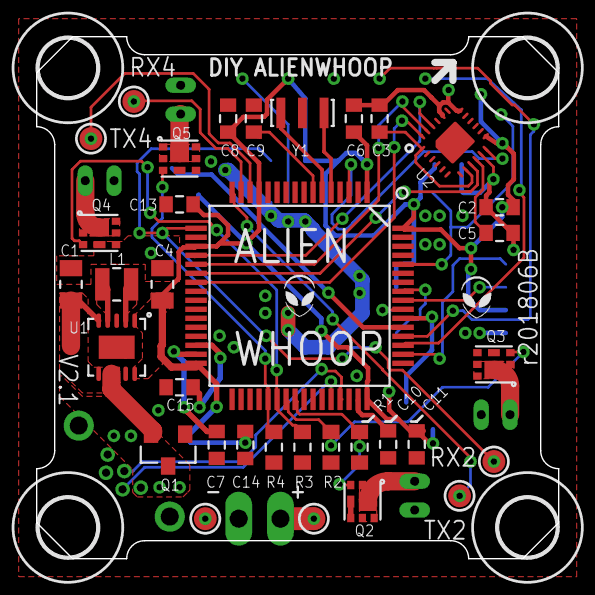
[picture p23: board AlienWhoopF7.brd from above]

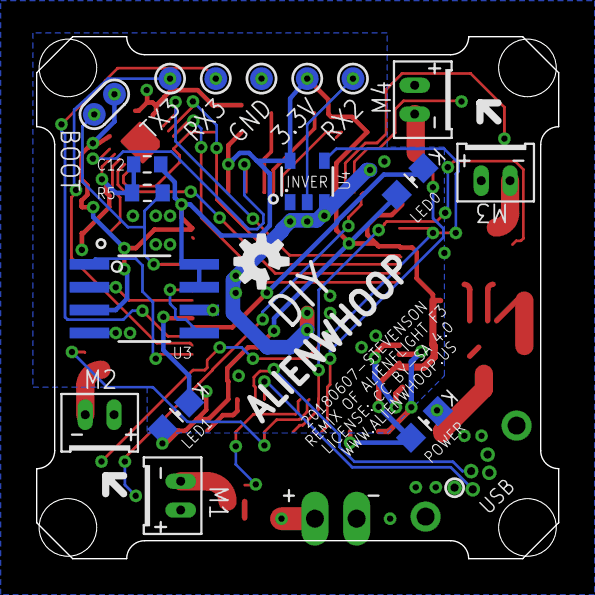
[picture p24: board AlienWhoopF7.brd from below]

Board: 2 copper layers, 29.0 x 29.0 mm, 59 parts (21 on the bottom side), 43 nets.

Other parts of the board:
U$1, U$2, U$3, U$4: 3,2

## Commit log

2017-08-11 Initial import of AlienWhoop F7 DIY MIX (backwards compatible to F4 processor). Graciously remixed from Lance's AlienFlight F3 Brushed Quad FC. Compatible with BetaFlight 3.2 RC1 and beyond. License: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
    [AlienWhoopF7.brd, AlienWhoopF7.sch, AlienWhoopF7_DIY_MIX_BoM.xlsx]
2018-06-08 Updated to V2.1 with Blackbox
    [AlienWhoopF7.brd, AlienWhoopF7.sch]

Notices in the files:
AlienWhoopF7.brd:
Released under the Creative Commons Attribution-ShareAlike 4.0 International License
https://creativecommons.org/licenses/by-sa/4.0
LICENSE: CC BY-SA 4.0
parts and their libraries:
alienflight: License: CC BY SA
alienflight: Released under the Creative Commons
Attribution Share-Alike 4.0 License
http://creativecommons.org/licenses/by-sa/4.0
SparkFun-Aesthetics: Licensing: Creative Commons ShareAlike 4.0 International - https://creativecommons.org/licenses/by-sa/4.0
